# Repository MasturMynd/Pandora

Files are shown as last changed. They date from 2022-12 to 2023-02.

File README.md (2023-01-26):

# Pandora

Have you ever been trying to add a mod to your V0 but quickly realize that it won't fit due to travel restrictions? Have you wanted to transition to a front mounted x rail but didn't want to lose Y travel? If you've said yes to either, allow me to present Pandora, a gantry mod for the Voron V0 that allows 142mm of X travel and 127mm of Y travel within the stock frame.

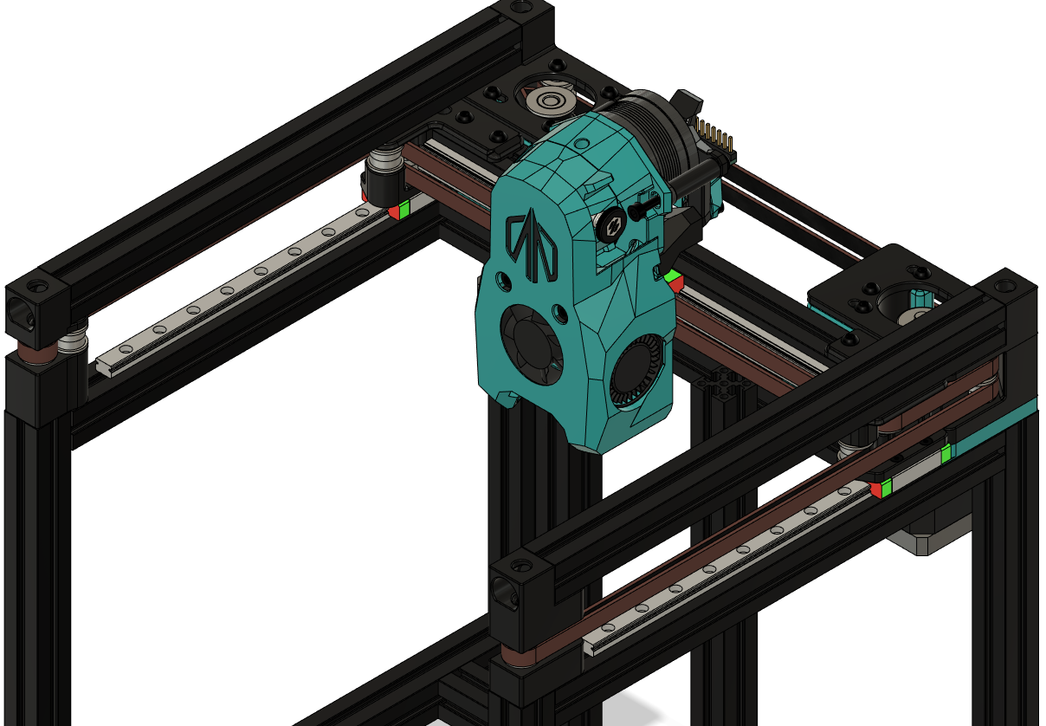
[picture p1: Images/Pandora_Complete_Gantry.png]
Image of Pandora Gantry


The Goal
---
I've been wanting to be able to incorporate a nozzle brush, purge bucket, sexbolt mod, etc., but there just wasn't enough travel with the stock gantry. The added travel outside the bounds of the bed should allow for a plethora of additional mods as well as a higher density of mods within the stock frame.

What's the Catch?
---
In order to use this mod you will need a new linear rail for X motion. In order to achieve 144mm of X travel, the stock 150mm rail won't cut it. The bearing block would fall off the rail before you hit full travel. On top of that, you'll also need some 3x14mm pins and a few extra F623 bearings. Aside from new parts you'll also have to account for the gantry being raised by ~8mm over stock. This means that the linear rails for Z motion may need to be raised and there's a possibility that things will get cramped under the tophat.

In addition, the stock side panel mounting will no longer work since the carriage for the Y rails protrudes over the extrusions. I highly recommend [Zero Panels](https://github.com/zruncho3d/ZeroPanels) as these add the extra room between the acrylic panels and the carriages with the added benefit of making panels easier to remove for cleaning and future upgrades.

The biggest hurdle for some is going to be that this setup currently requires sensorless homing. I am actively working to incorporate endstops into the design, but I refuse to sacrifice the additional travel that I've worked so hard to achieve.

BOM
---
| Part | Pandora | Stock | Diff | Sourcing |
| --- | --- | --- | --- | --- |
| **Front Idlers** | | | | | |
| 3x14mm Pin | 2 | 0 | 2 | [Amazon](https://www.amazon.com/uxcell-Stainless-Cylindrical-Support-Elements/dp/B07Y58JKMC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) |
| M3x8 BHCS | 2 | 2 | 0 | |
| M3x10 BHCS | 2 | 2 | 0 | |
| M3x40 BHCS | 2 | 0 | 2 | |
| M3 Washer | 8 | 4 | 4 | |
| M3 Hex Nut | 2 | 2 | 0 | |
| F623-RS | 8 | 4 | 4 | |
| | | | | |
| **XY Joints** | | | | | |
| M2x6 FHCS | 8 | 8 | 0 | |
| 3x14mm Pin | 2 | 0 | 2 | [Amazon](https://www.amazon.com/uxcell-Stainless-Cylindrical-Support-Elements/dp/B07Y58JKMC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) |
| M3x8 BHCS | 4 | 0 | 4 | |
| M3x10 BHCS | 2 | 0 | 2 | |
| M3x20 BHCS | 4 | 0 | 4 | |
| M3 Washer | 8 | 16 | 0 | |
| M3 Hex Nut | 6 | 6 | 0 | |
| M3 Threaded Insert | 2 | 4 | 2 | |
| F623-RS | 8 | 8 | 0 | |
| | | | | |
| **Drive Frames** | | | | | |
| M3x8 BHCS | 10 | 0 | 10 | |
| M3x10 BHCS | 2 | 2 | 0 | |
| M3x12 BHCS | 2 | 0 | 2 | |
| M3x25 BHCS | 4 | 0 | 4 | |
| M3x30 BHCS | 8 | 4 | 4 | |
| M3x35 BHCS | 4 | 20 | 0 | |
| M3x40 BHCS | 2 | 0 | 2 | |
| M3 Washer | 16 | 12 | 4 | |
| M3 Hex Nut | 10 | 10 | 0 | |
| M3 Threaded Insert | 10 | 8 | 10 | |
| F623-RS | 16 | 12 | 4 | |
| | | | | |
| **X Carriage** | | | | |
| MGN9-(H or C) Linear Guide Rail 180-200mm | 1 | 0 | 1 |[DFH](https://deepfriedhero.in/products/mgn9h-linear-rail?variant=40905213313193), [Amazon](https://www.amazon.com/gp/product/B07ZJMWGKH/,) |
| M3x8 BHCS | 4 | 0 | 4 | |
| M3x40 BHCS | 2 | 0 | 2 | |
| M3 Threaded Insert | 3 | 3 | 3 | |

After Installation
---
The first thing that you will want to do is head over to the Voron Design website to read about setting up sensorless homing. There's a fantastic article by none other than [clee](https://github.com/clee), [Setting Up and Calibrating Sensorless Homing](https://docs.vorondesign.com/community/howto/clee/sensorless_xy_homing.html).

Last, you'll want to ensure that your `printer.cfg` has been set up to take advantage of the extra room you've just unlocked without risking some sick high flying, mid air prints. You'll want to alter the `[stepper_x]` and `[stepper_y]` sections with the following machine limits:

```
[stepper_x]
...
position_endstop: 131
position_max: 131
position_min: -11
...

[stepper_y]
...
position_endstop: 125
position_max: 125
position_min: -2
...
```

Issues?
---
If you run into any trouble or have questions during assembly don't hesitate to ping me in the Voron Discord server (@Mastur_Mynd). Also, If you find any other sources for the above parts at comparative prices / quality (or better) please let me know!

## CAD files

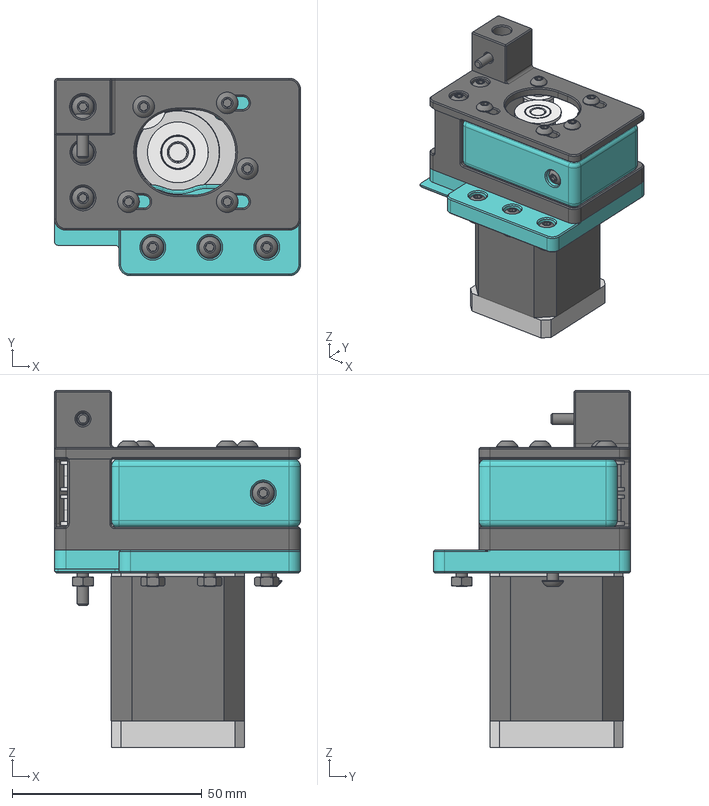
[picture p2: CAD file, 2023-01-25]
CAD/Drive_Frame-B.step
64.8 x 52.0 x 94.0 mm
drive_frame_lower(Mirror)
drive_frame_upper(Mirror)
[a]_drive_platform(Mirror)
Tensioner Housing(Mirror)
Tensioner Wedge(Mirror)
M3x8 BHCS v2(Mirror) x 5
M3x10 BHCS v2(Mirror)
M3x12 BHCS v5(Mirror)
M3x25 BHCS v5(Mirror) x 2
M3x30 BHCS v2(Mirror) x 4
M3x35 BHCS v4(Mirror) x 2
M3x40 BHCS v2(Mirror)
M3 Hex Nut v4(Mirror) x 5
M3 Threaded Insert v3(Mirror) x 5
NEMA14 52mm v3(Mirror)
GT2 20T 6mm(Mirror)
M3 Grub Screw(Mirror) x 2
f623-rs(Mirror) x 8
M3 washer-1(Mirror) x 8

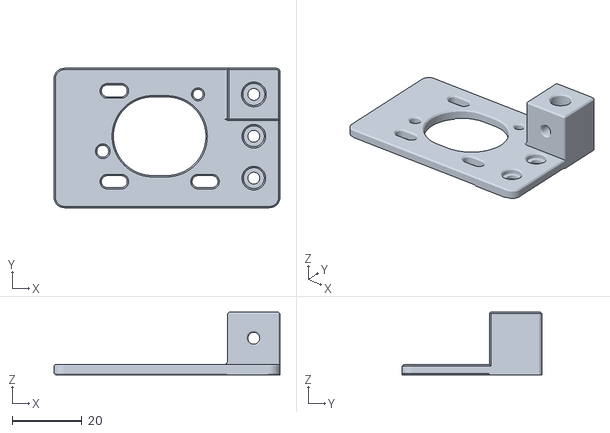
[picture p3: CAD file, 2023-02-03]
STLs/drive_frames/a_drive_frame_upper.stl
64.8 x 40.0 x 18.0

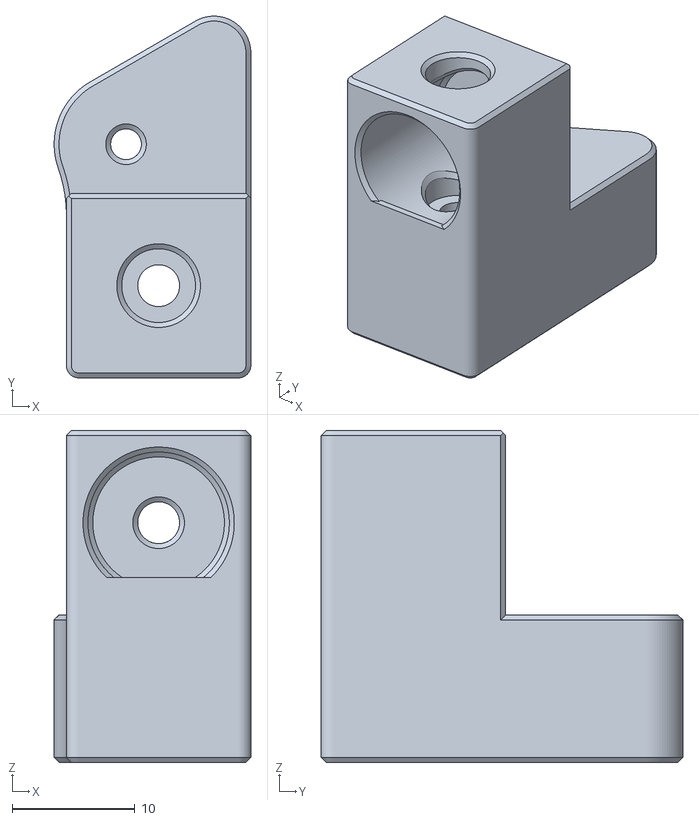
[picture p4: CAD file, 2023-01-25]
STLs/idlers/idler_right_upper.stl
16.0 x 29.4 x 27.0

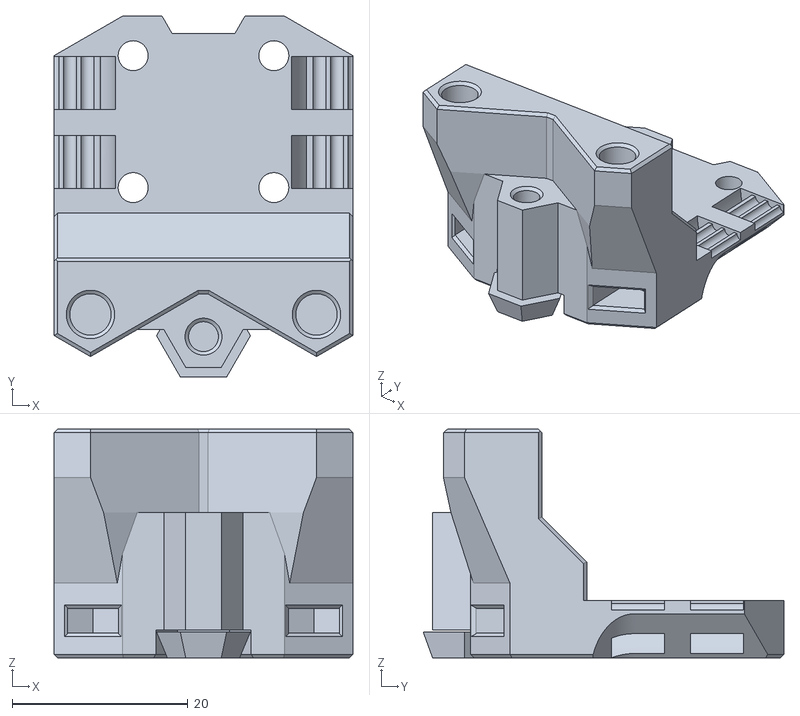
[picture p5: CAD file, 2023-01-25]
STLs/X_Carriage/MGN9-H_X_Carriage.stl
34.0 x 41.0 x 26.0

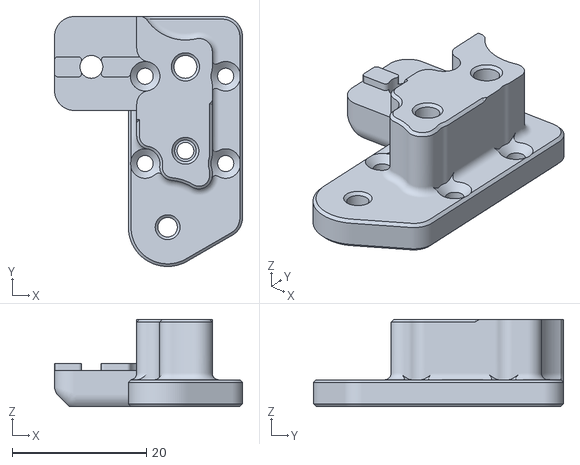
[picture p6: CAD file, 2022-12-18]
STLs/xy_joints/xy_joint_right_lower.stl
28.0 x 37.2 x 13.0

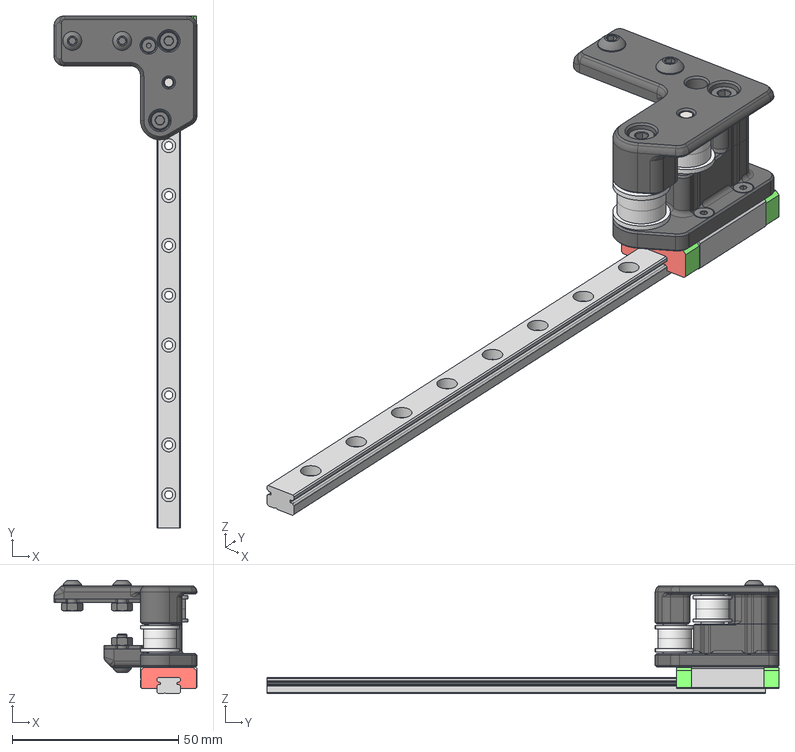
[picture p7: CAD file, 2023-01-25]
CAD/XY_Joint-Right.step
43.0 x 154.0 x 34.1 mm
Lower
Upper
LZE01-MGN7H-N-Z0_2
LZE01-MGN7H-150-NM-Z0_1
f623-rs x 4
M3 washer-1 x 4
M3x8 BHCS v2 x 2
M2x6 FHCS v2 x 4
M3x20 SHCS v2 x 2
M3x10 BHCS v2
3x14mm Pin v2
M3 Hex Nut v4 x 3
M3 Threaded Insert v3

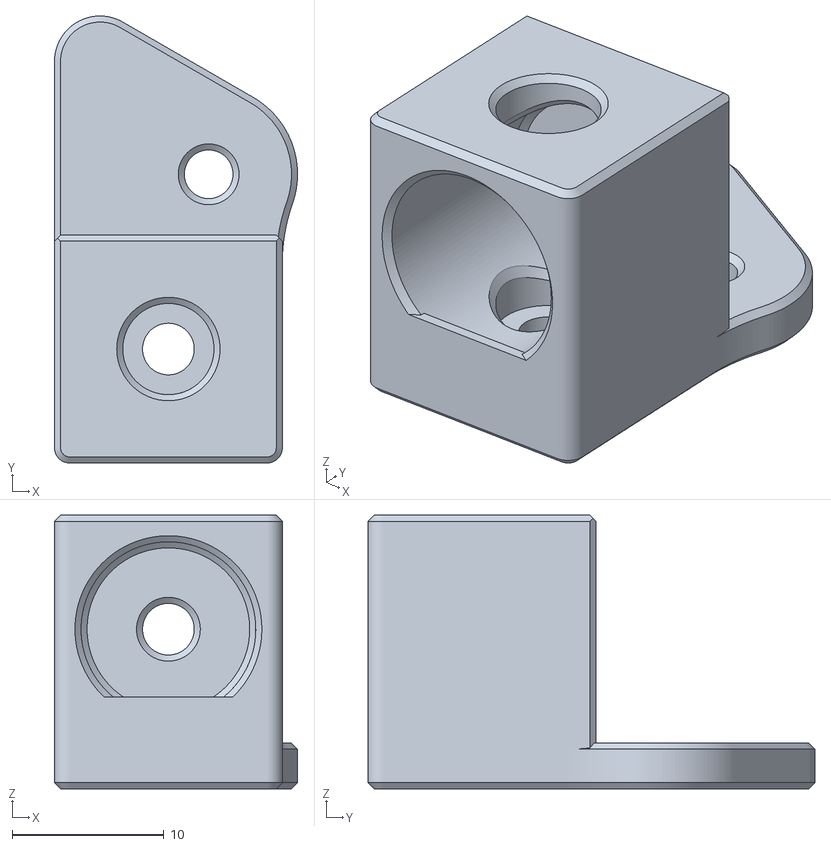
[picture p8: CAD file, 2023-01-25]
STLs/idlers/idler_left_upper.stl
16.0 x 29.4 x 18.0

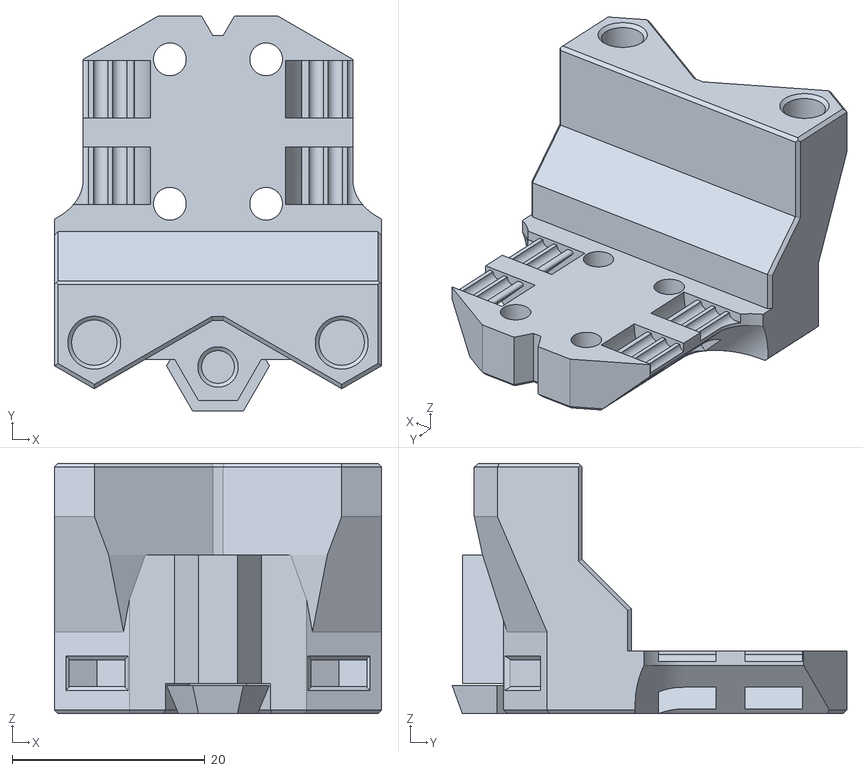
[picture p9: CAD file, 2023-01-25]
STLs/X_Carriage/MGN9-C_X_Carriage.stl
34.0 x 41.0 x 26.0

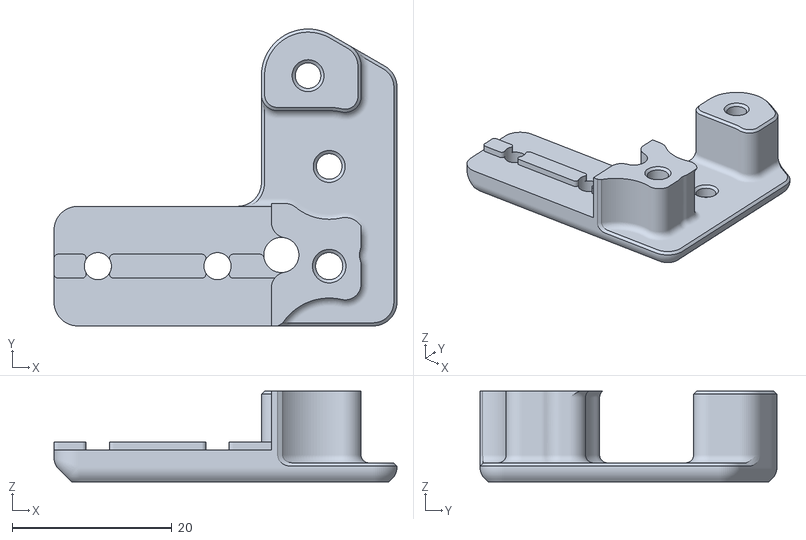
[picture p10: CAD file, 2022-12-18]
STLs/xy_joints/xy_joint_right_upper.stl
43.0 x 37.2 x 11.4

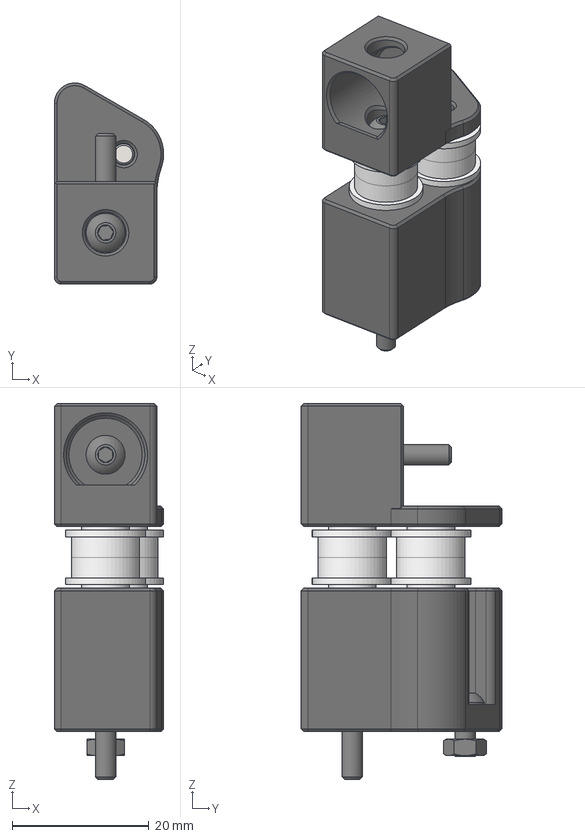
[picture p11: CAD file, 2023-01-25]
CAD/Idler-Left.step
16.0 x 29.4 x 55.0 mm
f623-rs x 4
M3 washer-1 x 4
M3x8 BHCS v2
M3x10 BHCS v2
M3x40 BHCS v2
M3 Hex Nut v4
3x14mm Pin v2

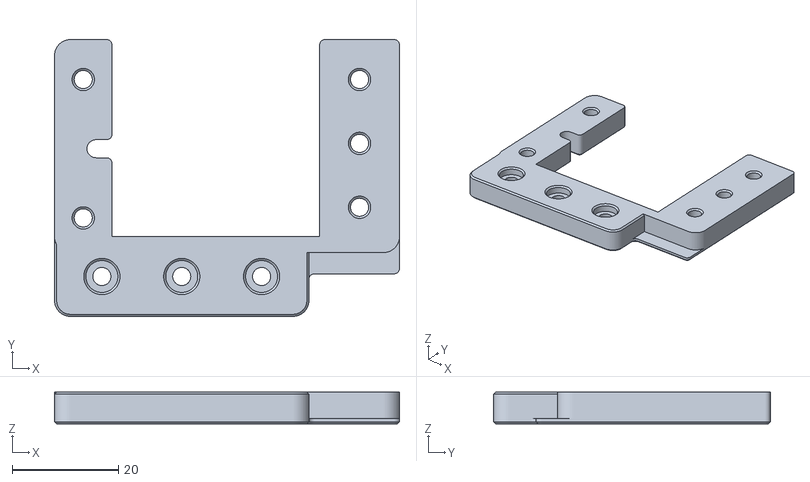
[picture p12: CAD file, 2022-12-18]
STLs/drive_frames/[a]_a_drive_platform.stl
64.8 x 52.0 x 6.00

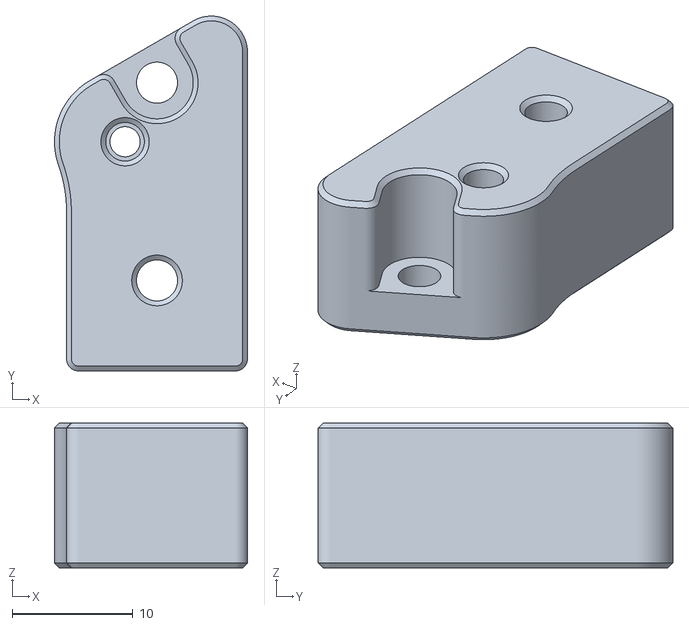
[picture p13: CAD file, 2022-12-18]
STLs/idlers/idler_right_lower.stl
16.0 x 29.4 x 12.0

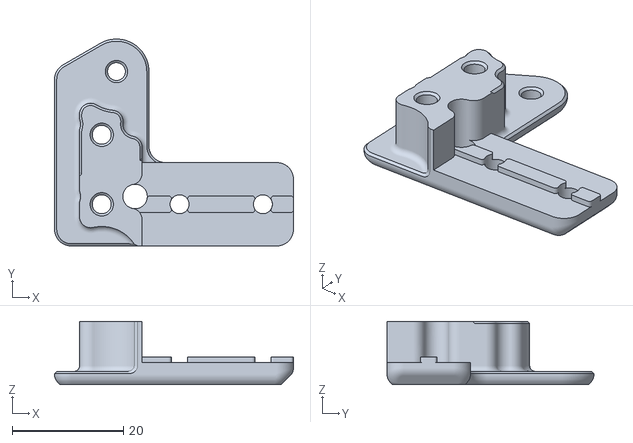
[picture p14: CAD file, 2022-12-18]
STLs/xy_joints/xy_joint_left_upper.stl
43.0 x 37.2 x 11.4

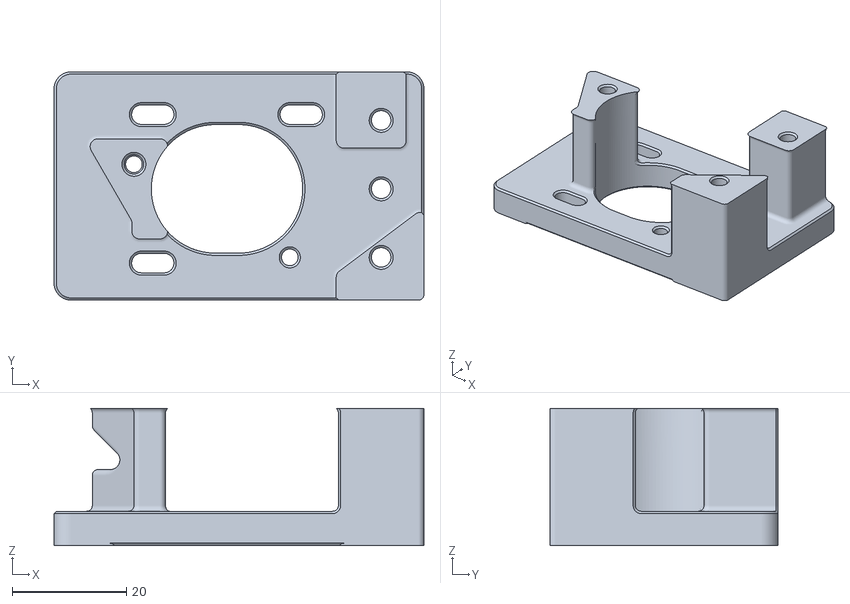
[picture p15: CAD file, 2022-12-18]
STLs/drive_frames/b_drive_frame_lower.stl
64.8 x 40.0 x 24.0

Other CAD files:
STLs/drive_frames/b_drive_frame_upper.stl
CAD/XY_Joint-Left.step
STLs/idlers/idler_left_lower.stl
STLs/xy_joints/xy_joint_left_lower.stl
CAD/Drive_Frame-A.step
CAD/Idler-Right.step
CAD/MGN9-C_X_Carriage.step
CAD/MGN9-H_X_Carriage.step
STLs/drive_frames/[a]_b_drive_platform.stl
STLs/drive_frames/[a]_tensioner_housing_x2.stl
STLs/drive_frames/[a]_tensioner_wedge_x2.stl
STLs/drive_frames/a_drive_frame_lower.stl

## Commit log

2022-08-28 Pre/Post Installation Guidance
    Added suggested prints for panel mounting as well as guidance for setting up sensorless homing and machine limits.
2022-08-28 Added spacer for optimal y rail placement
    [Y_Rail_Spacer.stl]
2022-08-28 No Longer Supporting MGN7 For X
    It doesn't make sense to purchase a lower quality rail when MGN9 is available for around the same price
    [XY_Joint_Left_MGN7_Lower.stl]
2022-08-28 No Longer Supporting MGN7
    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
    [XY_Joint_Right_MGN7_Upper.stl]
2022-08-28 Removed Heatsets / Corrected to BOM HW
    Removed the heatset for the bearing stack. Changed from M3x20 BHCS to M3x16 BHCS for the B idler.
    [A_Idler_Lower.stl, B_Idler_Lower.stl]
2022-08-28 Increased Pin Diameter
    Added 0.1mm of extra clearance for pins to be mounted in the lower portion of each joint.
    [XY_Joint_Left_MGN9_Lower.stl, XY_Joint_Right_MGN9_Lower.stl]
2022-08-28 Updated BOM For Individual Components
2022-08-29 Added Upper Panel Mounts for the Rear
    The stock corner rear mounts used a heatset insert that is no longer available due to raised belt paths. This will now use a longer screw and pass straight through from the panel mount, through the top motor mount, into the extrusion.
    [3mm_Top_Corner_Rear.stl, 3mm_Top_Corner_Rear_mirror.stl]
2022-09-02 Add pulley alignment jig
    [Pulley_Alignment_Jig.stl]
2022-12-18 Update to Revision 2
    Completely redesigned the gantry. Gained an additional mm of X travel and removed features that would conflict with stock V0 parts.
    [3mm_Top_Corner_Rear.stl, 3mm_Top_Corner_Rear_mirror.stl, A_Drive_Frame_Lower_x1.stl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]
2022-12-18 Corrected Orientation
    The B drive frame parts were inverted. Also added cross hatching for the recessed holes in the drive platforms.
    [[a]_a_drive_platform.stl, [a]_b_drive_platform.stl, b_drive_frame_lower.stl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]
2022-12-20 Corrected BOM
    M4x40 were listed by mistake. This has been corrected to M3x40
2022-12-20 Corrected BOM
2023-01-25 V0.2 Update
    The X carriages and front idlers have been updated for the Mini Stealthburner and camlocks for the hinged tophat.
    [Drive_Frame-A.step, Drive_Frame-B.step, Idler-Left.step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]
2023-01-26 Updated Amazon Link
    The old link was only offering 12mm or 18mm options
2023-02-03 Enlarged Tophat Holes
    The pin holes in the upper drive frames were causing V0.1 tophat lower corners to snap when disassembling.
    [a_drive_frame_upper.stl, b_drive_frame_upper.stl]
